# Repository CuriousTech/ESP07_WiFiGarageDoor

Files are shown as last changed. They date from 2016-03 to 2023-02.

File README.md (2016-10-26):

# ESP07_WiFiGarageDoor

This is USB powered and uses an analog IR range sensor (20 to 150cm) to detect door position on the top rail, and an HC-SR05 for the car, DC sink output for opener, OLED display, and DHT22 for temp and rh.
  
Note:  Pin 1 of the OLED is GND (these came from eBay, so I needed to use them for something).  
  
Here's [a small case](http://www.allelectronics.com/make-a-store/item/mbu-906/utility-case-2.74-x-1.99-x-0.83/1.html) that it fits nicely in.
  
UI

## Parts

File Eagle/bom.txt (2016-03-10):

OLED			0.96" I2C (Ground on pin 1 - eBay)
DHT22           ebay or anywhere
Sharp sensor	GP2Y0A02YK0F
Side tact		SKSCLBE010
R1-R3           10K 0806
R4				1K 0805
R5				5K6 (divider)
R6				4K7 (Convert Sharp sensors 2.8V to 1.0V)
C1-C3			0.1uF 0805
C4				1uF 0805
Q1			    NPN SOT-23
USB				Mini USB (common)
0.1" header		16 pins needed

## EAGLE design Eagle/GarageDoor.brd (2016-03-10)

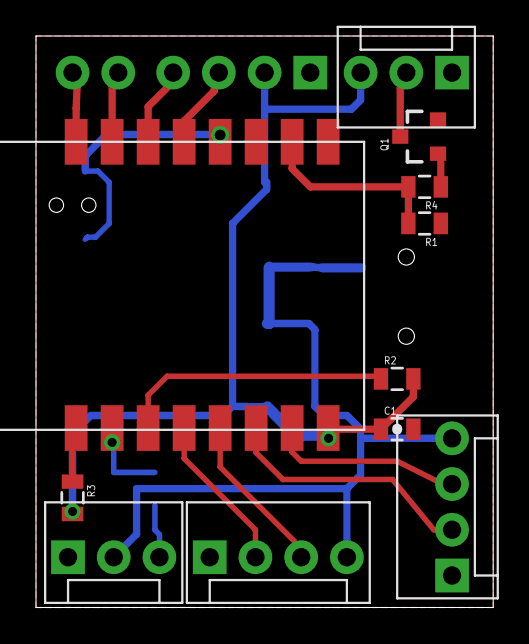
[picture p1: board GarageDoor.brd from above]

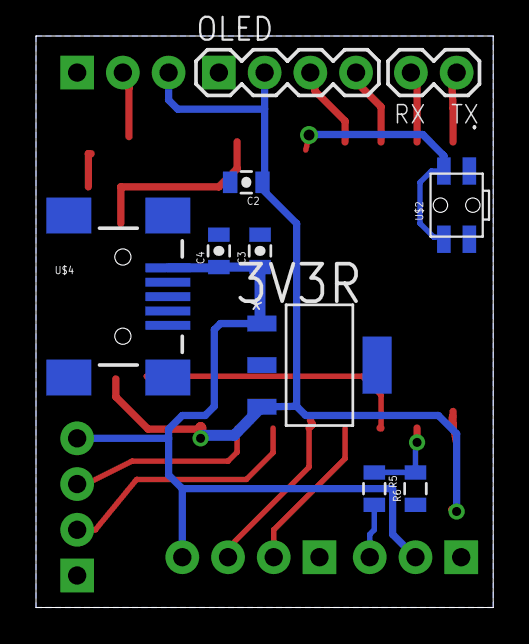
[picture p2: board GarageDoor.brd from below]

Board: 2 copper layers, 25.4 x 31.8 mm, 21 parts (10 on the bottom side), 19 nets.

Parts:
3V3R: MCP1824ST-3302E/DB; SOT230P700X180-4N
.: 1X02
C1, C2, C3: 0.1uF; 0805-CAP
C4: 1uF; 0805-CAP
JP1, JP3: MOLEX-1X4
JP2, JP6: MOLEX-1X3
OLED: 1X04
Q1: SOT23-3
R1, R2, R3: 10K; 0805
R4: 1K; 0805
R5: 5K6; 0805
R6: 4K7; 0805
U$1: ESP-07/12
U$2: SIDE-TACT
U$4: USB-MINIB-5PIN; USB-MINIB

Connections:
3V3: 3V3R.3, C1.1, C2.1, JP6.3, OLED.2, R2.2, R3.2, U$1.VCC
+5V: 3V3R.1, C3.1, C4.1, JP1.4, JP2.2, JP3.4, U$4.VBUS
ADC: R5.1, R6.2, U$1.ADC
ANA: JP2.3, R5.2
GND: 3V3R.2, 3V3R.4, C1.2, C2.2, C3.2, C4.2, JP1.1, JP2.1, JP3.1, JP6.1, OLED.1, Q1.2, R1.1, R6.1, U$1.GND, U$2.3, U$2.4, U$4.GND, U$4.MTN1, U$4.MTN2, U$4.MTN3, U$4.MTN4
ICSPCLK: R3.1, U$1.REST
IO0: U$1.GPIO0, U$2.1, U$2.2
IO12: JP1.2, U$1.GPIO12
IO13: JP1.3, U$1.GPIO13
IO14: JP3.3, U$1.GPIO14
IO15: R1.2, R4.2, U$1.GPIO15
IO16: JP3.2, U$1.GPIO16
unnamed: JP6.2, Q1.3
unnamed: OLED.4, U$1.GPIO4
unnamed: OLED.3, U$1.GPIO5
unnamed: Q1.1, R4.1
unnamed: R2.1, U$1.CH_PD
RXD: ..2, U$1.RXD
TXD: ..1, U$1.TXD

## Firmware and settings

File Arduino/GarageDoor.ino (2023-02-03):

/**The MIT License (MIT)

Copyright (c) 2016 by Greg Cunningham, CuriousTech

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
THE SOFTWARE IS PROVIDED "AS IS", WITHOUT WARRANTY OF ANY KIND, EXPRESS OR
IMPLIED, INCLUDING BUT NOT LIMITED TO THE WARRANTIES OF MERCHANTABILITY,
FITNESS FOR A PARTICULAR PURPOSE AND NONINFRINGEMENT. IN NO EVENT SHALL THE
AUTHORS OR COPYRIGHT HOLDERS BE LIABLE FOR ANY CLAIM, DAMAGES OR OTHER
LIABILITY, WHETHER IN AN ACTION OF CONTRACT, TORT OR OTHERWISE, ARISING FROM,
OUT OF OR IN CONNECTION WITH THE SOFTWARE OR THE USE OR OTHER DEALINGS IN THE
SOFTWARE.
*/

// Build with Arduino IDE 1.8.9, esp8266 SDK 2.5.0

//uncomment to enable Arduino IDE Over The Air update code
#define OTA_ENABLE
#define USE_OLED
#define DEBUG

//#define USE_SPIFFS // Uses 7K more program space

#include <Wire.h>
#ifdef USE_OLED
#include <ssd1306_i2c.h> // https://github.com/CuriousTech/WiFi_Doorbell/tree/master/Libraries/ssd1306_i2c
#endif

#include <EEPROM.h>
#include <ESP8266mDNS.h>
#include <ESPAsyncWebServer.h> // https://github.com/me-no-dev/ESPAsyncWebServer
#include "RunningMedian.h"
#include <TimeLib.h> // http://www.pjrc.com/teensy/td_libs_Time.html
#include <UdpTime.h>
#include "PushBullet.h"
#include "eeMem.h"
#include <JsonParse.h> // https://github.com/CuriousTech/ESP8266-HVAC/tree/master/Libraries/JsonParse
#include <JsonClient.h>
#ifdef OTA_ENABLE
#include <FS.h>
#include <ArduinoOTA.h>
#endif
#ifdef USE_SPIFFS
#include <FS.h>
#include <SPIFFSEditor.h>
#else
#include "pages.h"
#endif
#include "jsonstring.h"
#include <AM2320.h>
#include <NewPingESP8266.h>

int serverPort = 80;                    // port fwd for fwdip.php

#define ESP_LED  2  // low turns on ESP blue LED
#define MOTION  12  //
#define SR1     13  //
#define SWITCH  14
#define SR2     16  //
#define REMOTE  15

enum reportReason
{
  Reason_Setup,
  Reason_Status,
  Reason_Alert,
  Reason_Motion,
};

IPAddress lastIP;
IPAddress verifiedIP;
int nWrongPass;

#ifdef USE_OLED
SSD1306 display(0x3c, 5, 4); // Initialize the oled display for address 0x3c, sda=5, sdc=4
#endif

const char hostName[] ="GDO";

AM2320 am;

AsyncWebServer server( serverPort );
AsyncWebSocket ws("/ws"); // access at ws://[esp ip]/ws

PushBullet pb;

void jsonCallback(int16_t iName, int iValue, char *psValue);
JsonParse jsonParse(jsonCallback);
void jsonPushCallback(int16_t iEvent, uint16_t iName, int iValue, char *psValue);
JsonClient jsonPush(jsonPushCallback);

UdpTime utime;

float temp;
float rh;

eeMem ee;

bool bDoorOpen;
bool bCarIn;
bool bPulseRemote;
bool bMotion;
uint16_t doorVal;
uint16_t carVal;
uint16_t doorOpenTimer;
uint16_t doorDelay;
uint16_t displayTimer;

bool bConfigDone = false;
bool bStarted = false;
uint32_t connectTimer;

#define SONAR_NUM    2   // Number of sensors.
#define MAX_DISTANCE 400 // Maximum distance (in cm) to ping.

NewPingESP8266 sonar[SONAR_NUM] = {   // Sensor object array.
  NewPingESP8266(SR1, SR1, MAX_DISTANCE), // GDO 
  NewPingESP8266(SR2, SR2, MAX_DISTANCE)  // Car
};

String sDec(int t) // just 123 to 12.3 string
{
  String s = String( t / 10 ) + ".";
  s += t % 10;
  return s;
}

String dataJson()
{
  jsonString js("state");

  js.Var("t", (uint32_t)now() - ( (ee.tz + utime.getDST() ) * 3600) );
  js.Var("door", bDoorOpen);
  js.Var("car", bCarIn);
  js.Var("temp", String(temp/10 + ((float)ee.tempCal/10), 1) );
  js.Var("rh", String(rh/10, 1) );
  js.Var("o", ee.bEnableOLED);
  js.Var("carVal", carVal);         // use value to check for what your threshold should be
  js.Var("doorVal", doorVal);
  js.Var("motion", bMotion);
  return js.Close();
}

String settingsJson()
{
  jsonString js("settings");

  js.Var("ct",  ee.nCarThresh);
  js.Var("dt",  ee.nDoorThresh);
  js.Var("tz",  ee.tz);
  js.Var("at",  ee.alarmTimeout);
  js.Var("clt",  ee.closeTimeout);
  js.Var("delay", ee.delayClose);
  js.Var("rt", ee.rate);
  String s = String(ee.hostIP[0]);
  s += ".";
  s += String(ee.hostIP[1]);
  s += ".";
  s += String(ee.hostIP[2]);
  s += ".";
  s += String(ee.hostIP[3]);
  js.Var("host", s);
  js.Var("rt", ee.rate);
  return js.Close();
}

void displayStart()
{
  if(ee.bEnableOLED == false && displayTimer == 0)
  {
#ifdef USE_OLED
    display.init();
//    display.flipScreenVertically();
#endif
  }
  displayTimer = 30;
}

void parseParams(AsyncWebServerRequest *request)
{
  char password[64];
 
  if(request->params() == 0)
    return;

//  Serial.println("parseParams");

  // get password first
  for ( uint8_t i = 0; i < request->params(); i++ ) {
    AsyncWebParameter* p = request->getParam(i);

    String s = request->urlDecode(p->value());

    switch( p->name().charAt(0)  )
    {
      case 'k': // key
        s.toCharArray(password, sizeof(password));
        break;
    }
  }

  IPAddress ip = request->client()->remoteIP();

  if( ip && ip == verifiedIP ); // can skip if last verified
  else if( strcmp(password, ee.szControlPassword) || nWrongPass)
  {
    if(nWrongPass == 0) // it takes at least 10 seconds to recognize a wrong password
      nWrongPass = 10;
    else if((nWrongPass & 0xFFFFF000) == 0 ) // time doubles for every high speed wrong password attempt.  Max 1 hour
      nWrongPass <<= 1;
    if(ip != lastIP)  // if different IP drop it down
       nWrongPass = 10;

    jsonString js("hack");
    js.Var("ip", ip.toString() );
    js.Var("pass", password);
    ws.textAll(js.Close());

    lastIP = ip;
    return;
  }

  verifiedIP = ip;
  lastIP = ip;

  const char Names[][11]={
    "closedelay", // 0
    "closeto",
    "alarmto",
    "cal",
    "door",
    "oled",
    "rate",
    "reset",
    "pbt",
    "hostip",
    "port",
    "",
  };

  for ( uint8_t i = 0; i < request->params(); i++ ) {
    AsyncWebParameter* p = request->getParam(i);
    String s = request->urlDecode(p->value());
    bool which = (tolower(p->name().charAt(1) ) == 'd') ? 1:0;
    int val = s.toInt();

    uint8_t idx;
    for(idx = 0; Names[idx][0]; idx++)
      if( p->name().equals(Names[idx]) )
        break;

    switch( idx )
    {
      case 0: // close/open delay
          ee.delayClose = val;
          break;
      case 1: // close timeout (set a bit higher than it takes to close)
          ee.closeTimeout = val;
          break;
      case 2: // alarm timeout
          ee.alarmTimeout = val;
          break;
      case 3: // temp offset
          ee.tempCal = val;
          break;
      case 4: // Door (pulse the output)
          displayStart();
          if(val) doorDelay = ee.delayClose;
          else bPulseRemote = true;
          break;
      case 5: // OLED
        ee.bEnableOLED = (s == "true") ? true:false;
        if(!ee.bEnableOLED)
          displayTimer = 0;
#ifdef USE_OLED
        display.clear();
        display.display();
#endif
        break;
      case 6: // WS/event update rate
        ee.rate = val;
        break;
      case 7: // reset
        ESP.reset();
        break;
      case 8: // pushbullet
        s.toCharArray( ee.pbToken, sizeof(ee.pbToken) );
        break;
      case 9:
        if(s.length() > 9)
        {
          ee.hostPort = 80;
          ip.fromString(s.c_str());
        }
        else
          ee.hostPort = val ? val:80;
        ee.hostIP[0] = ip[0];
        ee.hostIP[1] = ip[1];
        ee.hostIP[2] = ip[2];
        ee.hostIP[3] = ip[3];
        CallHost(Reason_Setup, ""); // test
        break;
      case 10:
        ee.hostPort = val ? val:80;
        break;
    }
  }
}

// Time in hh:mm[:ss][AM/PM]
String timeFmt(bool do_sec, bool do_M)
{
  String r = "";
  if(hourFormat12() < 10) r = " ";
  r += hourFormat12();
  r += ":";
  if(minute() < 10) r += "0";
  r += minute();
  if(do_sec)
  {
    r += ":";
    if(second() < 10) r += "0";
    r += second();
    r += " ";
  }
  if(do_M)
  {
      r += isPM() ? "PM":"AM";
  }
  return r;
}

const char *jsonList1[] = {
  "key",
  "doorDelay", // close/open delay
  "closetimeout", // close timeout
  "alarmtimeout",
  "threshDoor",
  "threshCar",
  "door",
  "tempOffset",
  "oled",
  "TZ",
  NULL
};

bool bKeyGood;
bool bDataMode;

void jsonCallback(int16_t iName, int iValue, char *psValue)
{
  if(bKeyGood == false && iName > 0)
    return;  // only allow key set

  switch(iName)
  {
    case 0: // key
      if(!strcmp(psValue, ee.szControlPassword)) // first item must be key
        bKeyGood = true;
      break;
    case 1: // doorDelay
      ee.delayClose = iValue;
      break;
    case 2: // closeTimeout
      ee.closeTimeout = iValue;
      break;
    case 3:
      ee.alarmTimeout = iValue;
      break;
    case 4: // threshDoor
      ee.nDoorThresh = iValue;
      break;
    case 5: // threshCar
      ee.nCarThresh = iValue;
      break;
    case 6: // Door
      displayStart();
      if(iValue) doorDelay = ee.delayClose;
      else bPulseRemote = true; // start output pulse
      break;
    case 7: // tempOffset
      ee.tempCal = iValue;
      break;
    case 8: // OLED
      ee.bEnableOLED = iValue ? true:false;
      break;
    case 9: // TZ
      ee.tz = iValue;
      break;
  }
}

const char *jsonListPush[] = { "",
  "time", // 0
  NULL
};

uint8_t failCnt;

void jsonPushCallback(int16_t iEvent, uint16_t iName, int iValue, char *psValue)
{
  switch(iEvent)
  {
    case -1: // status
      if(iName >= JC_TIMEOUT)
      {
        if(++failCnt > 5)
          ESP.restart();
      }
      else failCnt = 0;
      break;
    case 0: // time
      switch(iName)
      {
        case 0: // time
          setTime(iValue + ( (ee.tz + utime.getDST() ) * 3600));
          break;
      }
      break;
  }
}

void CallHost(reportReason r, String sStr)
{
  if(ee.hostIP[0] == 0 || WiFi.status() != WL_CONNECTED) // no host set
    return;

  String sUri = String("/wifi?name=\"GDO\"&reason=");

  switch(r)
  {
    case Reason_Setup:
      sUri += "setup&port="; sUri += serverPort;
      break;
    case Reason_Status:
      sUri += "status&door="; sUri += bDoorOpen;
      sUri += "&car="; sUri += bCarIn;
      sUri += "&temp="; sUri += String(temp/10,1);
      sUri += "&rh="; sUri += String(rh/10,1);
      break;
    case Reason_Alert:
      sUri += "alert&value=\"";
      sUri += sStr;
      sUri += "\"";
      break;
    case Reason_Motion:
      sUri += "motion";
      break;
  }

  IPAddress ip(ee.hostIP);
  String url = ip.toString();
  jsonPush.begin(url.c_str(), sUri.c_str(), ee.hostPort, false, false, NULL, NULL);
  jsonPush.addList(jsonListPush);
}

void onWsEvent(AsyncWebSocket * server, AsyncWebSocketClient * client, AwsEventType type, void * arg, uint8_t *data, size_t len)
{  //Handle WebSocket event
  static bool bRestarted = true;
  String s;

  switch(type)
  {
    case WS_EVT_CONNECT:      //client connected
      if(bRestarted)
      {
        bRestarted = false;
        client->text( "{\"cmd\":\"alert\",\"text\":\"Restarted\"}" );
      }
      client->keepAlivePeriod(50);
      client->text( dataJson() );
      client->text( settingsJson() );
      client->ping();
      break;
    case WS_EVT_DISCONNECT:    //client disconnected
      break;
    case WS_EVT_ERROR:    //error was received from the other end
      break;
    case WS_EVT_PONG:    //pong message was received (in response to a ping request maybe)
      break;
    case WS_EVT_DATA:  //data packet
      AwsFrameInfo * info = (AwsFrameInfo*)arg;
      if(info->final && info->index == 0 && info->len == len){
        //the whole message is in a single frame and we got all of it's data
        if(info->opcode == WS_TEXT){
          data[len] = 0;

          uint32_t ip = client->remoteIP();

          bKeyGood = (ip && verifiedIP == ip) ? true:false; // if this IP sent a good key, no need for more
          jsonParse.process((char*)data);
          if(bKeyGood)
            verifiedIP = ip;
        }
      }
      break;
  }
}

void setup()
{
  pinMode(MOTION, INPUT);
  pinMode(ESP_LED, OUTPUT);
  pinMode(REMOTE, OUTPUT);
  pinMode(SWITCH, OUTPUT);
  digitalWrite(ESP_LED, LOW);
  digitalWrite(REMOTE, LOW);
  digitalWrite(SWITCH, HIGH);

  // initialize dispaly
#ifdef USE_OLED
  display.init();
//  display.flipScreenVertically();
  display.clear();
  display.display();
#else
  am.begin(5, 4);
#endif

#ifdef DEBUG
  Serial.begin(115200);
//  delay(3000);
  Serial.println();
  Serial.println();
#endif

  WiFi.hostname(hostName);
  WiFi.mode(WIFI_STA);

  if ( ee.szSSID[0] )
  {
    WiFi.begin(ee.szSSID, ee.szSSIDPassword);
    WiFi.setHostname(hostName);
    bConfigDone = true;
  }
  else
  {
    Serial.println("No SSID. Waiting for EspTouch.");
    WiFi.beginSmartConfig();
  }
  connectTimer = now();

#ifdef USE_SPIFFS
  SPIFFS.begin();
  server.addHandler(new SPIFFSEditor("admin", controlPassword));
#endif

  // attach AsyncWebSocket
  ws.onEvent(onWsEvent);
  server.addHandler(&ws);

  server.on( "/", HTTP_GET | HTTP_POST, [](AsyncWebServerRequest *request){
    bDataMode = false; // turn off numeric display and frequent updates
  });
  server.on ( "/iot", HTTP_GET | HTTP_POST, [](AsyncWebServerRequest *request )
  {
    bDataMode = false; // turn off numeric display and frequent updates
    parseParams(request);
#ifdef USE_SPIFFS
    request->send(SPIFFS, "/index.html");
#else
    request->send_P(200, "text/html", page1);
#endif
  });
  server.on( "/setup.html", HTTP_GET | HTTP_POST, [](AsyncWebServerRequest *request){
    parseParams(request);
    bDataMode = true;
#ifdef USE_SPIFFS
    request->send(SPIFFS, "/setup.html");
#else
    request->send_P(200, "text/html", page2);
#endif
  });
  server.on( "/s", HTTP_GET | HTTP_POST, [](AsyncWebServerRequest *request){
    parseParams(request);

    String page = "{\"ip\": \"";
    page += WiFi.localIP().toString();
    page += ":";
    page += serverPort;
    page += "\"}";
    request->send( 200, "text/json", page );
  });
  server.on( "/json", HTTP_GET | HTTP_POST, [](AsyncWebServerRequest *request){
    parseParams(request);
    request->send( 200, "text/json", settingsJson() );
  });
  server.on("/heap", HTTP_GET, [](AsyncWebServerRequest *request){
    request->send(200, "text/plain", String(ESP.getFreeHeap()));
  });
  server.on("/favicon.ico", HTTP_GET, [](AsyncWebServerRequest *request){
    AsyncWebServerResponse *response = request->beginResponse_P(200, "image/x-icon", favicon, sizeof(favicon));
    response->addHeader("Content-Encoding", "gzip");
    request->send(response);
  });

  server.onNotFound([](AsyncWebServerRequest *request){
//    request->send(404);
  });

  server.onFileUpload([](AsyncWebServerRequest *request, String filename, size_t index, uint8_t *data, size_t len, bool final){
  });
  server.onRequestBody([](AsyncWebServerRequest *request, uint8_t *data, size_t len, size_t index, size_t total){
  });

  server.begin();

#ifdef OTA_ENABLE
  ArduinoOTA.setHostname(hostName);
  ArduinoOTA.begin();
#endif

  jsonParse.setList(jsonList1);
  digitalWrite(ESP_LED, HIGH);
  if(ee.rate == 0) ee.rate = 60;
}

uint16_t stateTimer = ee.rate;

void sendState()
{
  ws.textAll(dataJson());
  stateTimer = ee.rate;
}

RunningMedian<uint16_t, 12> rangeMedian[2];
RunningMedian<uint16_t, 20> tempMedian[2];

void loop()
{
  static uint8_t hour_save, sec_save;
  static uint8_t cnt = 0;
  static uint16_t oldCarVal, oldDoorVal;
  bool bNew;
  static bool bReleaseRemote;
  static bool bClear;

  MDNS.update();
#ifdef OTA_ENABLE
  ArduinoOTA.handle();
#endif
  
  if(WiFi.status() == WL_CONNECTED && ee.useTime)
    utime.check(ee.tz);

  if(bDataMode && (carVal != oldCarVal || doorVal != oldDoorVal) ) // high speed update
  {
    oldCarVal = carVal;
    oldDoorVal = doorVal;
    ws.textAll( dataJson() );
  }

  if(digitalRead(MOTION) != bMotion)
  {
    bMotion = digitalRead(MOTION);
    if(bMotion)
    {
      displayStart();
      sendState();
      CallHost(Reason_Motion,"");
    }
  }

  if(sec_save != second()) // only do stuff once per second (loop is maybe 20-30 Hz)
  {
    sec_save = second();

    if(!bConfigDone)
    {
      if( WiFi.smartConfigDone())
      {
        Serial.println("SmartConfig set");
        bConfigDone = true;
        connectTimer = now();
      }
    }
    if(bConfigDone)
    {
      if(WiFi.status() == WL_CONNECTED)
      {
        if(!bStarted)
        {
          Serial.println("WiFi Connected");
          MDNS.begin( hostName );
          bStarted = true;

          CallHost(Reason_Setup, "");
          if(ee.useTime)
            utime.start();

          MDNS.addService("iot", "tcp", serverPort);
          WiFi.SSID().toCharArray(ee.szSSID, sizeof(ee.szSSID)); // Get the SSID from SmartConfig or last used
          WiFi.psk().toCharArray(ee.szSSIDPassword, sizeof(ee.szSSIDPassword) );
        }
      }
      else if(now() - connectTimer > 10) // failed to connect for some reason
      {
        Serial.println("Connect failed. Starting SmartConfig");
        connectTimer = now();
        ee.szSSID[0] = 0;
        WiFi.mode(WIFI_AP_STA);
        WiFi.beginSmartConfig();
        bConfigDone = false;
        bStarted = false;
      }
    }

    float av;
    rangeMedian[1].getAverage(2, av);
    doorVal = av;

    bNew = (doorVal < ee.nDoorThresh) ? true:false;
    if(bNew != bDoorOpen)
    {
      displayStart();
      bDoorOpen = bNew;
      doorOpenTimer = bDoorOpen ? ee.alarmTimeout : 0;
      sendState();
      CallHost(Reason_Status,"");
    }

    rangeMedian[0].getAverage(2, av);
    carVal = av;
    bNew = (carVal < ee.nCarThresh) ? true:false; // lower is closer

    if(carVal < 15) // something is < 25cm away
    {
      displayStart();
    }

    if(bNew != bCarIn)
    {
      bCarIn = bNew;
      if(bCarIn)
      {
        displayStart();
      }
      sendState();
      CallHost(Reason_Status,"");
    }

    if (hour_save != hour())
    {
      hour_save = hour();
      if((hour_save&1) == 0)
        CallHost(Reason_Setup,"");
      CallHost(Reason_Status,"");
      if(hour_save == 2 && ee.useTime)
      {
        utime.start(); // update time daily at DST change
      }
      ee.update(); // update EEPROM if needed while we're at it (give user time to make many adjustments)
    }

    if(second() == 58) // 2 seconds before
      digitalWrite(SWITCH, LOW);
    else if(second() == 0)
    {
      float temp2, rh2;
      if(am.measure(temp2, rh2))
      {
        digitalWrite(SWITCH, HIGH);
        tempMedian[0].add( (1.8 * temp2 + 32.0) * 10 );
        tempMedian[0].getAverage(2, temp2);
        tempMedian[1].add(rh2 * 10);
        tempMedian[1].getAverage(2, rh2);
        if(temp != temp2)
        {
          temp = temp2;
          rh = rh2;
          sendState();
          CallHost(Reason_Status,"");
        }
      }
      display.init();
    }

    if(nWrongPass)
      nWrongPass--;

    if(bReleaseRemote) // reset remote output 1 second after it started
    {
      digitalWrite(REMOTE, LOW);
      bReleaseRemote = false;
    }
    if(bPulseRemote)
    {
      if(bDoorOpen == false) // closing door
      {
         doorOpenTimer = ee.closeTimeout; // set the short timeout
      }
//      Serial.println("pulseRemote");
      digitalWrite(REMOTE, HIGH);
      bPulseRemote = false;
      bReleaseRemote = true;
    }

    if(doorDelay) // delayed close/open
    {
      if(--doorDelay == 0)
        bPulseRemote = true;
    }

    if(doorOpenTimer && doorDelay == 0) // door open watchdog
    {
      if(--doorOpenTimer == 0)
      {
        CallHost(Reason_Alert, "Door not closed");
        ws.textAll( "{\"cmd\":\"alert\",\"text\":\"Door not closed\"}" );
        pb.send("GDO", "Door not closed", ee.pbToken);
      }
    }

    if(--stateTimer == 0) // a 60 second keepAlive
      sendState();

    if(displayTimer) // temp display on thing
      displayTimer--;

    uint8_t x = (second() & 3);
  
    // draw the screen here
    display.clear();
    if(ee.bEnableOLED || displayTimer)
    {
      display.drawPropString(x, 0, timeFmt(true, true) );
  
      if(bDataMode) // display numbers when the setup page is loaded
      {
        display.drawPropString(x+ 2, 23, String(doorVal) );
        display.drawPropString(x+80, 23, String(carVal) ); // cm
      }
      else  // normal status
      {
        display.drawPropString(x+ 2, 23, bDoorOpen ? "Open":"Closed" );
        display.drawPropString(x+80, 23, bCarIn ? "In":"Out" );
      }
      display.drawPropString(x+2, 47, String(temp/10 + ((float)ee.tempCal/10), 1) + "]");
      display.drawPropString(x+64, 47, String(rh/10, 1) + "%");
    }
    display.display();
  }

  static uint32_t rangeTime;
  static uint8_t bTog;
  if(millis() - rangeTime >= 100) {
    rangeTime = millis();
    uint16_t ul = sonar[bTog].ping_cm();
    rangeMedian[bTog].add( ul );
    bTog = bTog ? 0:1;
  }
}

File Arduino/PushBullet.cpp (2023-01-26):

/*
  PushBullet.cpp - Arduino library for sending a pushbullet push.
  Copyright 2016 Greg Cunningham, CuriousTech.net

  This library is free software; you can redistribute it and/or modify it under the terms of the GNU GPL 2.1 or later.
*/

#include "PushBullet.h"
#include "jsonstring.h"
const char host[] = "api.pushbullet.com";
const char url[] = "/v2/pushes";

// Initialize instance with a callback (event list index, name index from 0, integer value, string value)
PushBullet::PushBullet()
{
  m_ac.onConnect([](void* obj, AsyncClient* c) { (static_cast<PushBullet*>(obj))->_onConnect(c); }, this);
  m_ac.onDisconnect([](void* obj, AsyncClient* c) { (static_cast<PushBullet*>(obj))->_onDisconnect(c); }, this);
  m_ac.onError([](void* obj, AsyncClient* c, int8_t error) { (static_cast<PushBullet*>(obj))->_onError(c, error); }, this);
  m_ac.onTimeout([](void* obj, AsyncClient* c, uint32_t time) { (static_cast<PushBullet*>(obj))->_onTimeout(c, time); }, this);
  m_ac.onData([](void* obj, AsyncClient* c, void* data, size_t len) { (static_cast<PushBullet*>(obj))->_onData(c, static_cast<char*>(data), len); }, this);

  m_ac.setRxTimeout(10000);
}

bool PushBullet::send(const char *pTitle, String sBody, const char *pToken)
{
  strncpy(m_szTitle, pTitle, sizeof(m_szTitle) );
  sBody.toCharArray(m_szBody, sizeof(m_szBody) );
  strncpy(m_szToken, pToken, sizeof(m_szToken) );

  if(m_ac.connected())
    m_ac.stop();

  return m_ac.connect( host, 443);//, true);// set ASYNC_TCP_SSL_ENABLED to 1 in ESPAsyncTCP/src/async_config.h
}
  
void PushBullet::_onDisconnect(AsyncClient* client)
{
  (void)client;
}

void PushBullet::_onTimeout(AsyncClient* client, uint32_t time)
{
  (void)client;
}

void PushBullet::_onError(AsyncClient* client, int8_t error)
{
  (void)client;

  Serial.print("PB error ");
  Serial.println(error);
}

void PushBullet::_onConnect(AsyncClient* client)
{
  (void)client;

  jsonString js;
  js.Var("type", "note");
  js.Var("title", m_szTitle);
  js.Var("body", m_szBody);
  String data = js.Close();

  String s = String("POST ");
  s += url;
  s += " HTTP/1.1\r\n";
  s += "Host: ";
  s += host;
  s += "\r\n"
       "Content-Type: application/json\r\n"
       "Access-Token: ";
  s += m_szToken;
  s += "\r\n"
       "User-Agent: Arduino\r\n"
       "Content-Length: ";
  s += data.length();
  s += "\r\n"
       "Connection: close\r\n\r\n";
  s += data;
  s += "\r\n\r\n";

  m_ac.add(s.c_str(), s.length());
}

void PushBullet::_onData(AsyncClient* client, char* data, size_t len)
{
  (void)client;

// Lots of data gets sent back
//  Serial.println("PB onData");
//  Serial.print(data);
}

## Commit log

2016-01-06 Changed to positive side sensor control
    [GarageDoor.brd]
2016-01-29 Changed to NPN output
    [GarageDoor.brd]
2016-01-31 Car distance was flipped
    [GarageDoor.ino]
2016-02-04 Bugs found after power outages
2016-03-10 Simplified, added DHT22
    [GarageDoor.brd]
2016-03-13 Switched to esp time
2016-09-18 Added delay timer
2016-09-22 Switched to ESPAsyncWebServer
2016-09-22 Switched to ESPAsyncWebServer retry
2017-07-06 Fix for printfAll bug in latest WebSocket
    [GarageDoor.ino]
2018-05-01 Removed a printf, flipped screen
    [GarageDoor.ino]

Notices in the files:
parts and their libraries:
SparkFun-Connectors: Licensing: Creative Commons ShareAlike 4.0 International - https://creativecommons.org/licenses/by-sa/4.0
